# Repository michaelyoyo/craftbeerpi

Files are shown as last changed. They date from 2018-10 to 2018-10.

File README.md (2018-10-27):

# CraftBeerPi

This project is shamelessly forked from https://github.com/Manuel83/craftbeerpi

This fork is intended to add support for a few new sensors and for my custom HERMS
controller PCB.

The PCB contains
-2x MAX31865 RTD Amplifiers
-1x EzoPh Amplifier
-2x Pump/Heater Outputs
-A bunch of LEDs
-Automatic control of a 12v Power Supply
-An expansion connector because I can't think of everything

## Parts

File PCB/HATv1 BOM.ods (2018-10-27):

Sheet: HATv1
Part | Value | Package | Description | Source/PN | Footprint correct? | Notes
C1 | 0.1uF | 0603 | 5v buck boost | have | y
C2 | 100uF | PANASONIC_E | Main input filter cap | have | y | --Probably need more capacitance (6A max input current...) | -Check package
C3 | 10uF | 0805 | Buck filter cap | have | y
C4 | 0.1uF | 0603 | buck filter cap | have | y
C5 | 22uF | 1210 | buck output cap | have | y
C6 | 22uF | 1210 | buck output cap | have | y
C7 | 22uF | 1210 | buck output cap | have | y
C8 | 75pF | 0603 | buck ff cap | have | y
C9 | 10uF | 0805 | 3.3vsb ldo input | have | y
C10 | 1uF | 0603 | 3.3vsb ldo output | have | y
C11 | 47uF | 3528 | rPi 5v input | have | y | -1206
C12 | 0.1uF | 0603 | eeprom decoupling | have | y
C13 | 0.1uF | 0603 | pwm decoupling | have | y
C14 | 3.3u | 0603 | isense1 filter | have | y
C15 | 3.3u | 0603 | isense2 filter | have | y
C16 | 0.1u | 0603 | rtd1 decoupling | have | y
C17 | 0.1u | 0603 | rtd1 decoupling | have | y
C18 | 0.1u | 0603 | rtd2 decoupling | have | y
C19 | 0.1u | 0603 | rtd2 decoupling | have | y
C20 | 100n | 0603 | rtd1 filter | have | y
C21 | 100n | 0603 | rtd2 filter | have | y
C22 | 10uF | 1206 | ezoph decoupling | have | y
D1 | 250mA/100V | SMA | pump1 flyback | have | y
D2 | 250mA/100V | SMA | pump2 flyback | have | y
F1 | 7.5A | 1206 | main input | 693-3413.0224.22 | y
F2 | 1A | 1206 | 5vbuck input | 530-0ZCG0150BF2C | y
F3 | 25mA | 1206 | 3.3vsb input | have | y |  | -I have 50mA through hole fuses
J1 |  |  | 6pin PSU input | 710-691305140006 | y | 710-691363110006
J4 | 20 Pin low profile smt header | 2x20 0.1” Header | rpi header | 200-HLE12002GDVA | y
J5 | 1.27mm | 24pin 0.05” FFC | expansion connector | 538-502244-2430 | y | 538-15021-0424
J6 |  | 5mm Terminal Block | pump1 | 710-691305140002 | y | 710-691363110002
J7 |  | 5mm Terminal Block | pump2 | 710-691305140002 | y | 710-691363110002
J8 |  | 3pin Molex | rtd1 | 538-22-04-1031 | y | 538-22-01-1032 | 538-08-50-0113-CT
J9 |  | 3pin Molex | rtd2 | 538-22-04-1031 | y | 538-22-01-1032
J10 | BNCPTH | BNC | ezoph | have | y
L1 | 33uH | srp1265a | 5v buck | have | y
LED1 | red | 0603 | adc alert (pump overcurrent) | 859-LTST-C191KRKT | y
LED2 | green | 0603 | gpled0 | have | y
LED3 | red | 0603 | gpled1 | 859-LTST-C191KRKT | y
LED4 | green | 0603 | rtd1 good | have | y
LED5 | green | 0603 | rtd2 good | have | y
LED6 | green | 0603 | phgood | have | y
LED7 | blue | 0603 | 3.3v rail | have | y
LED8 | blue | 0603 | 5v rail | have | y
LED9 | blue | 0603 | 12v rail | have | y
Q1 | MOSFETSON5X6 | SON5X6MM | pump1 | have | y
Q2 | MOSFETSON5X6 | SON5X6MM | pump2 | have | y
Q3 | 220mA/50V/3.5Î© | SOT23-3 | adc alert | 621-DMG6968U-7 | y
R1 | 511k | 0603 | 5v buck enable | have | y
R2 | 49.9 | 0603 | 5v buck feedback | have | y | <1%
R3 | 100k | 0603 | 5v buck enable | have | y
R4 | 100k | 0603 | 5v buck feedback | have | y | <1%
R5 | 13.3k | 0603 | 5v buck feedback | have | y | <1%
R6 | 180 | 0603 | pon opto current limit | have | y
R7 | 887k | 0603 | pon delay div set | 660-RN73H1JTD8873B25 | y | <1%
R8 | 715k | 0603 | pon delay set | 660-RN73H1JD7233F100 | y | 725k, make sure it still works
R9 | 1M | 0603 | pon delay div set | have | y | <1%
R10 | 3.9k | 0603 | i2c pullup | have | y
R11 | 3.9k | 0603 | i2c pullup | have | y
R12 | 1k | 0603 | eeprom wp pullup | have | y
R13 | 3.9k | 0603 | eeprom i2c pullup | have | y
R14 | 3.9k | 0603 | eeprom i2c pullup | have | y
R15 | 180 | 0603 | led ilim | have | y | -all leds, calculate proper current limit
R16 | 180 | 0603 | led ilim | have | y
R17 | 180 | 0603 | led ilim | have | y
R18 | 180 | 0603 | led ilim | have | y
R19 | 180 | 0603 | led ilim | have | y
R20 | 180 | 0603 | led ilim | have | y
R21 | 50m | 1206 | pump1 shunt | 588-LVK12R050DER | y | <.5%
R22 | 50m | 1206 | pump2 shunt | 588-LVK12R050DER | y | <.5%
R23 | 180 | 0603 | led ilim | have | y
R24 | 180 | 0603 | led ilim | have | y
R25 | 180 | 0603 | led ilim | have | y
R26 | 3.3k | 0603 | adc alert pullup | have | y
R27 | 330 | 0603 | isense1 filter | have | y | <1%
R28 | 330 | 0603 | isense2 filter | have | y | <1%
R29 | 400 .1% | 0603 | rtd1 reference | 71-PAT0603E4000BST1 | y | <.1%
R30 | 400 .1% | 0603 | rtd2 reference | 71-PAT0603E4000BST1 | y | <.1%
S1 |  | 12mm Tact Switch PTH | pon switch | 611-PTS125SK85LFS | y
U1 |  | SOT23-6 | 5v buck | have | y
U2 | NCP715 | SC70 | 3.3vsb ldo | 863-NCP715SQ33T2G | y
U3 | LT6994 | SOT23-6 | pon off delay | 584-C6994MPS6-1TMPF | y
U4 | ILD213T-IDL213T | SO08 | pon opto | 782-ILD213T | y
U5 | LT4358LTC4358CFE | TSSOP-16 | rPi ideal diode | 584-LTC4358CFE#PBF | y
U6 | CAT24C256 | SO8 | rPi eeprom | have | y
U7 | PCA9685 | TSSOP-28_4MM | 16-channel 12-bit PWM | have | y
U8 | ADS1015 | MSOP10 | ADS1015 12-BIT ADC | have | y
U9 | MAX31865 | TQFN20 | rtd1 | sample from maxim | y
U10 | MAX31865 | TQFN20 | rtd2 | sample from maxim | y
U11 | EZOPH | EZOPH | ph measurement | have | y | -update footprint

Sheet: Sheet2
R6 | 180 | 0603 | pon opto current limit | have | y
R15 | 180 | 0603 | led ilim | have | y | -all leds, calculate proper current limit
R16 | 180 | 0603 | led ilim | have | y
R17 | 180 | 0603 | led ilim | have | y
R18 | 180 | 0603 | led ilim | have | y
R19 | 180 | 0603 | led ilim | have | y
R20 | 180 | 0603 | led ilim | have | y
R23 | 180 | 0603 | led ilim | have | y
R24 | 180 | 0603 | led ilim | have | y
R25 | 180 | 0603 | led ilim | have | y
R27 | 330 | 0603 | isense1 filter | have | y | <1%
R28 | 330 | 0603 | isense2 filter | have | y | <1%
R10 | 3.9k | 0603 | i2c pullup | have | y
R11 | 3.9k | 0603 | i2c pullup | have | y
R13 | 3.9k | 0603 | eeprom i2c pullup | have | y
R14 | 3.9k | 0603 | eeprom i2c pullup | have | y

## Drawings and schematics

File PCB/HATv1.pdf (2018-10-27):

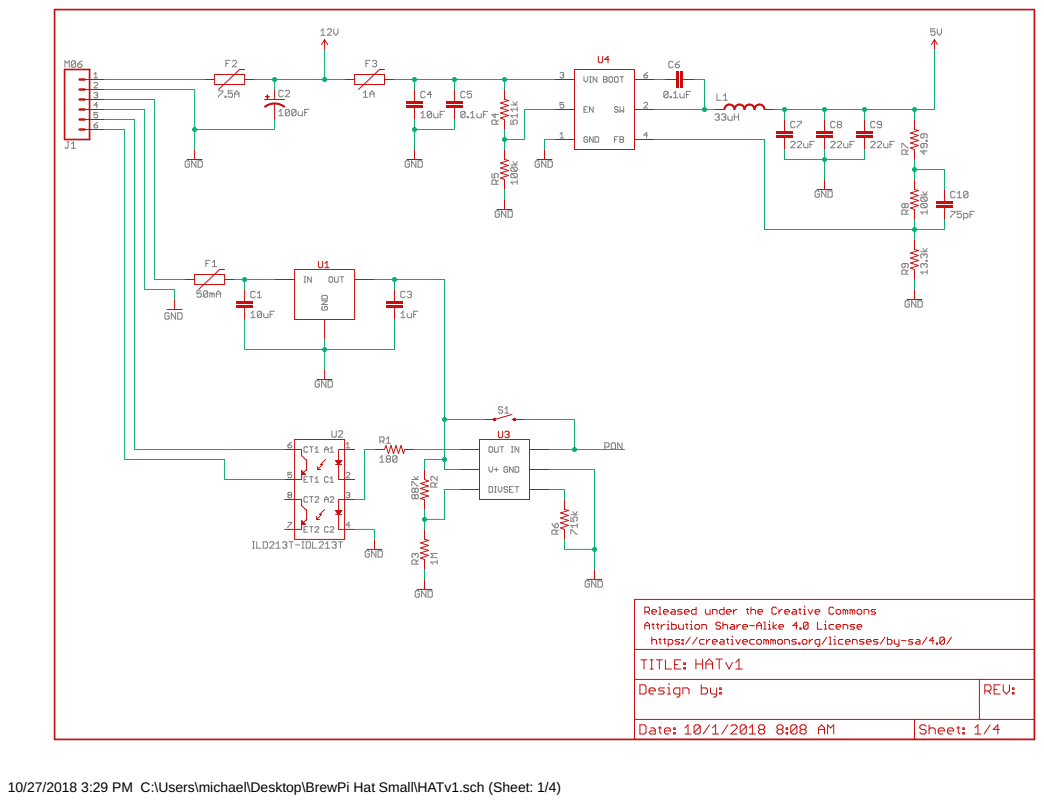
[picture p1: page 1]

10/27/2018 3:29 PM C:\Users\michael\Desktop\BrewPi Hat Small\HATv1.sch (Sheet: 1/4)

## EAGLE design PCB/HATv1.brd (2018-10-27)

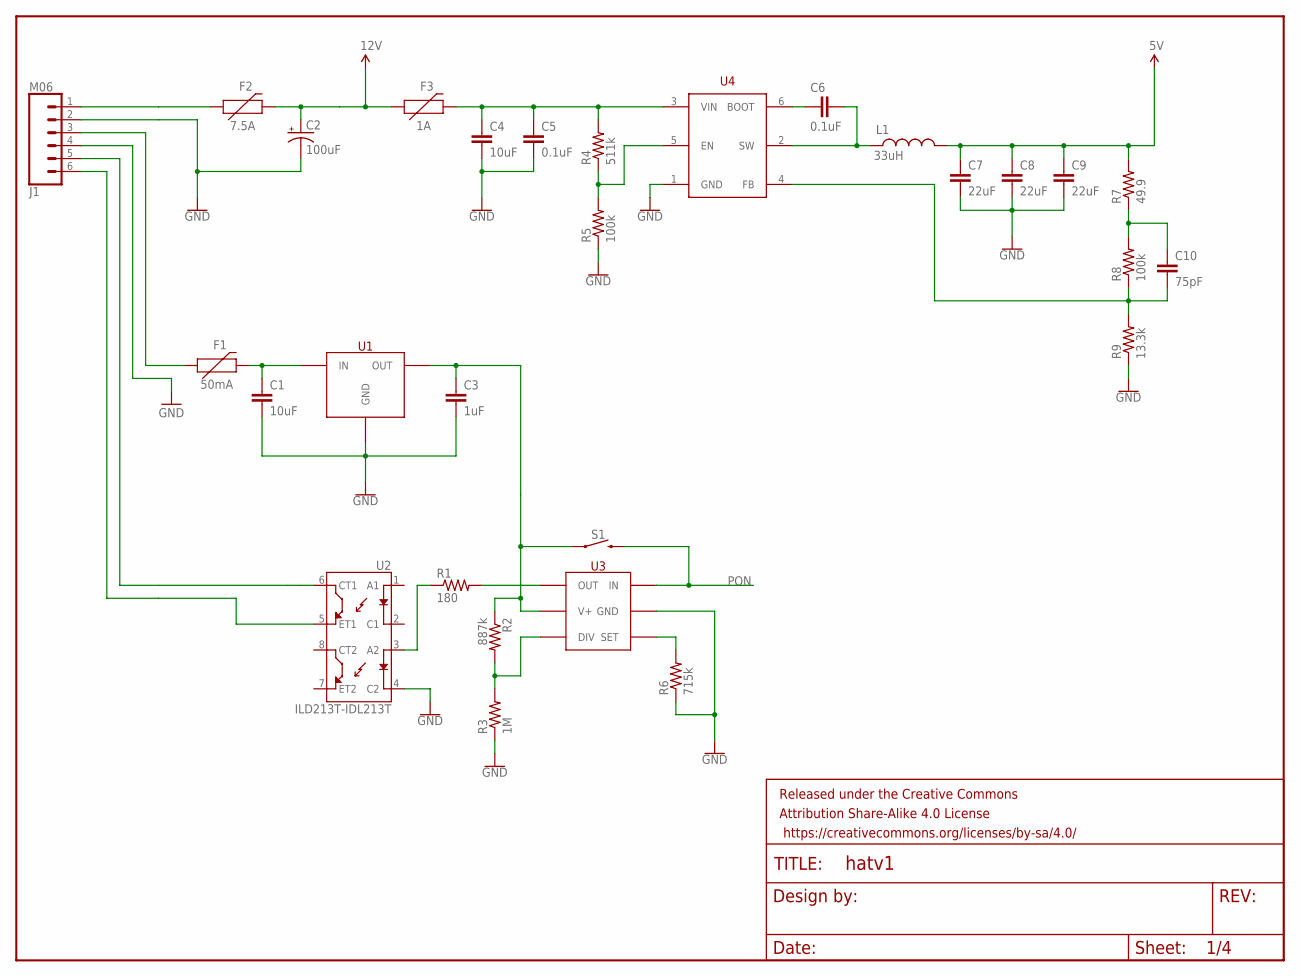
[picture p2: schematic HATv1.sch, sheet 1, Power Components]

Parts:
C1, C4: 10uF; 0805
C2: 100uF; PANASONIC_E
C3: 1uF; 0603-CAP
C5, C6: 0.1uF; 0603-CAP
C7, C8, C9: 22uF; 1210
C10: 75pF; 0603-CAP
F1: 50mA; PTH
F2: 7.5A; 1206
F3: 1A; 2010
FRAME1: FRAME-LETTERNO_PACKAGE; DUMMY
J1: M06; SCREWTERMINAL-3.5MM-6
L1: 33uH; SRP1265A
R1: 180; 0603-RES
R2: 887k; 0603-RES
R3: 1M; 0603-RES
R4: 511k; 0603-RES
R5, R8: 100k; 0603-RES
R6: 715k; 0603-RES
R7: 49.9; 0603-RES
R9: 13.3k; 0603-RES
S1: MOMENTARY-SWITCH-SPST-SMD-12MM; TACTILE_SWITCH_SMD_12MM
U1: NCP715; SC70
U2: ILD213T-IDL213T; SO08
U3: LT6994; SOT23-6
U4: TPS54302; SOT23-6

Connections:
5V: C7.1, C8.1, C9.1, L1.P$2 (2), R7.2; also elsewhere on the board
12V: C2.+, F2.2, F3.1; also elsewhere on the board
GND: C1.2, C2.-, C3.2, C4.2, C5.2, C7.2, C8.2, C9.2, J1.2, J1.4, R3.1, R5.1, R6.1, R9.1, U1.2 (GND), U2.4 (C2), U3.2 (GND), U4.1 (GND); also elsewhere on the board
unnamed: R1.1, U2.3 (A2)
unnamed: C6.1, U4.6 (BOOT)
unnamed: C6.2, L1.P$1 (1), U4.2 (SW)
unnamed: C10.1, R7.1, R8.2
unnamed: C10.2, R8.1, R9.2, U4.4 (FB)
unnamed: R4.1, R5.2, U4.5 (EN)
unnamed: J1.6, U2.5 (ET1)
unnamed: J1.5, U2.6 (CT1)
unnamed: R1.2, U3.6 (OUT)
unnamed: R2.2, R3.2, U3.4 (DIV)
unnamed: R6.2, U3.3 (SET)
unnamed: C3.1, R2.1, S1.1, U1.5 (OUT), U3.5 (V+)
unnamed: C1.1, F1.P$2 (2), U1.4 (IN)
unnamed: F1.P$1 (1), J1.3
unnamed: C4.1, C5.1, F3.2, R4.2, U4.3 (VIN)
unnamed: F2.1, J1.1
PON: S1.3 (2), U3.1 (IN); also elsewhere on the board

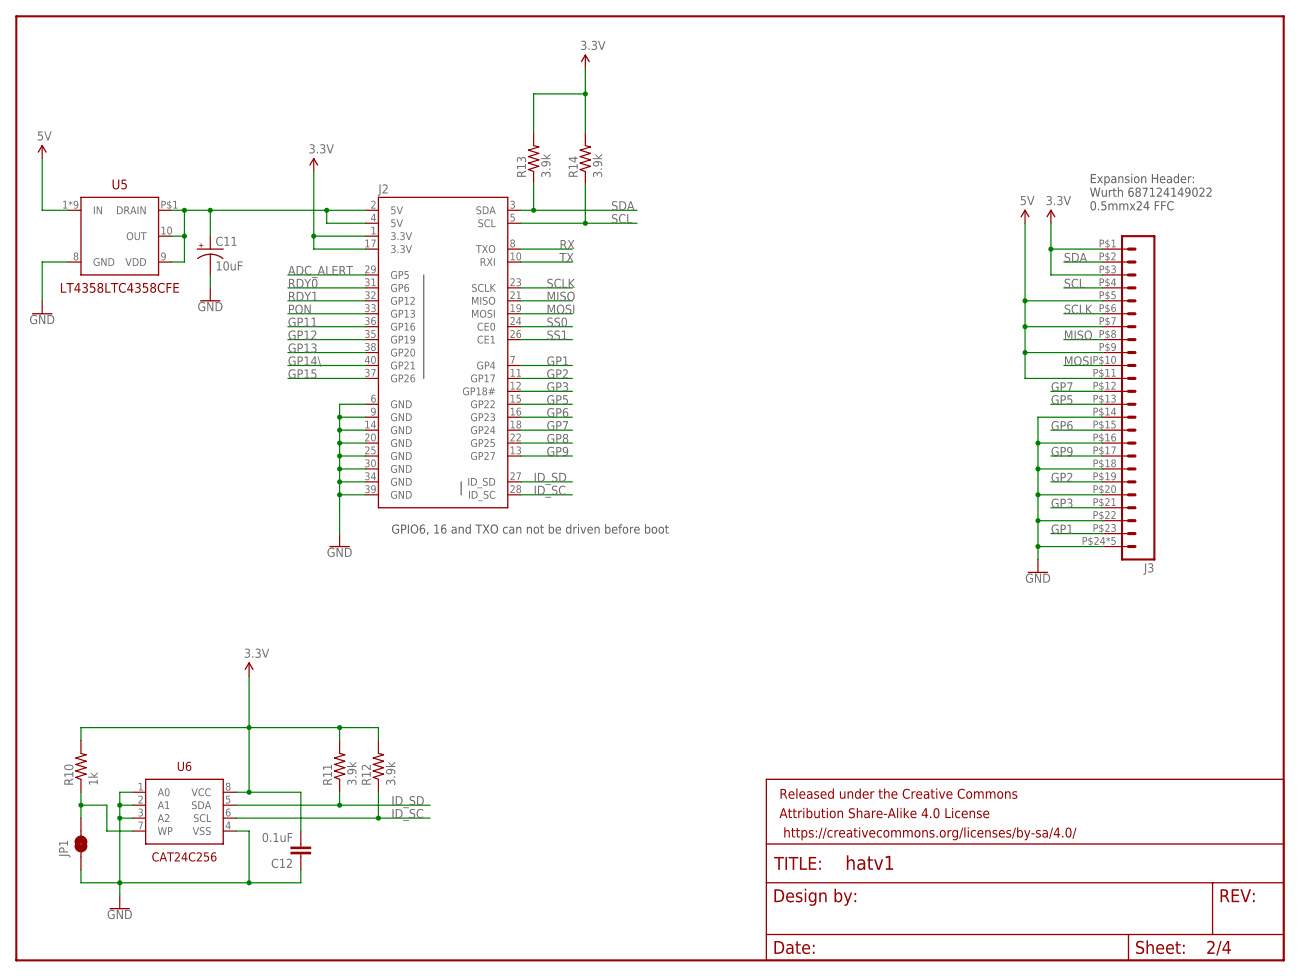
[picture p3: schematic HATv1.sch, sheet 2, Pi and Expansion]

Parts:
C11: 10uF; EIA3216
C12: 0.1uF; 0603-CAP
FRAME2: FRAME-LETTERNO_PACKAGE; DUMMY
J2: RASPBERRYPI-40-PIN-GPIO2X20PASSTHROUGH; 1X24SAMTEC
J3: M24FFC; FFC_24
JP1: JUMPER-PAD-2-NC_BY_TRACE; PAD-JUMPER-2-NC_BY_TRACE_YES_SILK
R10: 1k; 0603-RES
R11, R12, R13, R14: 3.9k; 0603-RES
U5: LT4358LTC4358CFE; TSSOP-16
U6: CAT24C256; SO8

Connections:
3.3V: C12.2, J2.1 (3.3V), J2.17 (3.3V), J3.P$1 (2), J3.P$3 (4), R10.2, R11.2, R12.2, R13.2, R14.2, U6.8 (VCC); also elsewhere on the board
5V: J3.P$5 (6), J3.P$7 (8), J3.P$9 (10), J3.P$11 (12), U5.1 (IN), U5.2 (IN), U5.3 (IN), U5.4 (IN), U5.12 (IN), U5.13 (IN), U5.14 (IN), U5.15 (IN), U5.16 (IN); also elsewhere on the board
ADC_ALERT: J2.29 (GP5); also elsewhere on the board
GND: C11.-, C12.1, J2.6 (GND), J2.9 (GND), J2.14 (GND), J2.20 (GND), J2.25 (GND), J2.30 (GND), J2.34 (GND), J2.39 (GND), J3.P$14 (15), J3.P$16 (17), J3.P$18 (19), J3.P$20 (21), J3.P$22 (23), J3.P$24 (25), J3.P$25 (25), J3.P$26 (25), J3.P$27 (25), J3.P$28 (25), JP1.1, U5.8 (GND), U6.1 (A0), U6.2 (A1), U6.3 (A2), U6.4 (VSS); also elsewhere on the board
GP1: J2.7 (GP4), J3.P$23 (24)
GP2: J2.11 (GP17), J3.P$19 (20)
GP3: J2.12 (GP18#), J3.P$21 (22)
GP5: J2.15 (GP22), J3.P$13 (14)
GP6: J2.16 (GP23), J3.P$15 (16)
GP7: J2.18 (GP24), J3.P$12 (13)
GP8: J2.22 (GP25)
GP9: J2.13 (GP27), J3.P$17 (18)
GP11: J2.36 (GP16)
GP12: J2.35 (GP19)
GP13: J2.38 (GP20)
GP14\: J2.40 (GP21)
GP15: J2.37 (GP26)
ID_SC: J2.28 (ID_SC), R12.1, U6.6 (SCL)
ID_SD: J2.27 (ID_SD), R11.1, U6.5 (SDA)
MISO: J2.21 (MISO), J3.P$8 (9); also elsewhere on the board
MOSI: J2.19 (MOSI), J3.P$10 (11); also elsewhere on the board
unnamed: JP1.2, R10.1, U6.7 (WP)
unnamed: C11.+, J2.2 (5V), J2.4 (5V), U5.9 (VDD), U5.10 (OUT), U5.P$1 (DRAIN)
PON: J2.33 (GP13); also elsewhere on the board
RDY0: J2.31 (GP6); also elsewhere on the board
RDY1: J2.32 (GP12); also elsewhere on the board
RX: J2.8 (TXO); also elsewhere on the board
SCL: J2.5 (SCL), J3.P$4 (5), R14.1; also elsewhere on the board
SCLK: J2.23 (SCLK), J3.P$6 (7); also elsewhere on the board
SDA: J2.3 (SDA), J3.P$2 (3), R13.1; also elsewhere on the board
SS0: J2.24 (CE0); also elsewhere on the board
SS1: J2.26 (CE1); also elsewhere on the board
TX: J2.10 (RXI); also elsewhere on the board

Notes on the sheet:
GPIO6, 16 and TXO can not be driven before boot
Expansion Header: Wurth 687124149022 0.5mmx24 FFC

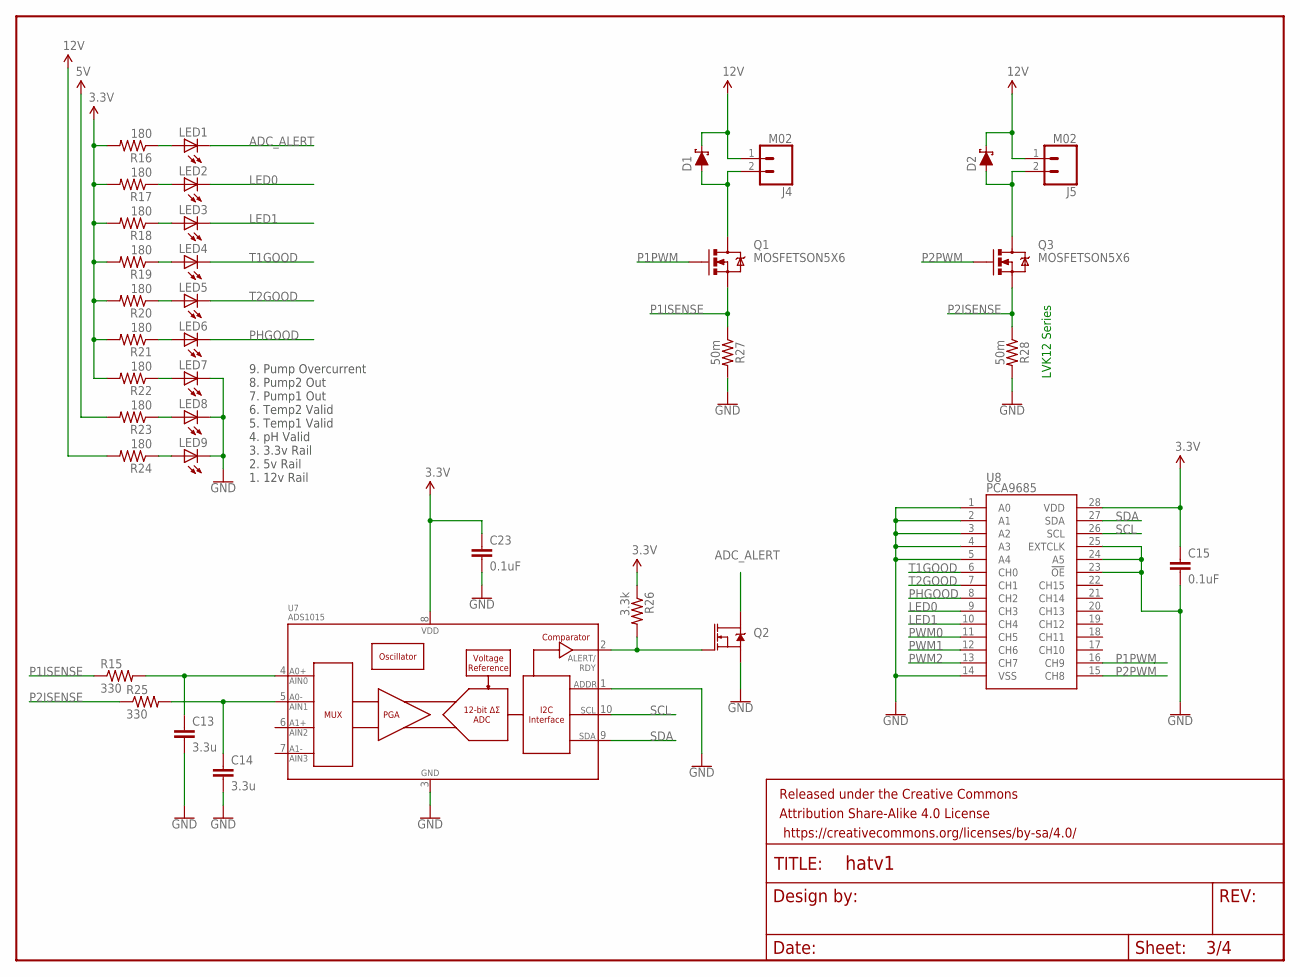
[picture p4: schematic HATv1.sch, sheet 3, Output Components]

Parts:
C13, C14: 3.3u; 0603
C15, C23: 0.1uF; 0603-CAP
D1, D2: DIODE-SCHOTTKY-B340A; SMA-DIODE
FRAME3: FRAME-LETTERNO_PACKAGE; DUMMY
J4, J5: M02; SCREWTERMINAL-3.5MM-2
LED1, LED2, LED3, LED4, LED5, LED6, LED7, LED8, LED9: LEDCHIP-LED0603; CHIP-LED0603
Q1, Q3: MOSFETSON5X6; SON5X6MM
Q2: MOSFET-NCH-BSS138; SOT23-3
R15, R25: 330; 0603-RES
R16, R17, R18, R19, R20, R21, R22, R23, R24: 180; 0603-RES
R26: 3.3k; 0603-RES
R27, R28: 50m; 1206
U7: ADS1015; MSOP10
U8: PCA9685; TSSOP-28_4MM

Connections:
3.3V: C15.1, C23.1, R16.2, R17.2, R18.2, R19.2, R20.2, R21.2, R22.2, R26.1, U7.8 (VDD), U8.28 (VDD); also elsewhere on the board
5V: R23.2; also elsewhere on the board
12V: D1.C, D2.C, J4.1, J5.1, R24.2; also elsewhere on the board
ADC_ALERT: LED1.C, Q2.3 (D); also elsewhere on the board
GND: C13.2, C14.2, C15.2, C23.2, LED7.C, LED8.C, LED9.C, Q2.2 (S), R27.2, R28.2, U7.1 (ADDR), U7.3 (VSS), U8.1 (A0), U8.2 (A1), U8.3 (A2), U8.4 (A3), U8.5 (A4), U8.14 (VSS), U8.23 (!OE), U8.24 (A5), U8.25 (EXTCLK); also elsewhere on the board
LED0: LED2.C, U8.9 (CH3)
LED1: LED3.C, U8.10 (CH4)
unnamed: LED1.A, R16.1
unnamed: D1.A, J4.2, Q1.P$5 (D), Q1.P$6 (D), Q1.P$7 (D), Q1.P$8 (D), Q1.P$9 (D)
unnamed: D2.A, J5.2, Q3.P$5 (D), Q3.P$6 (D), Q3.P$7 (D), Q3.P$8 (D), Q3.P$9 (D)
unnamed: C13.1, R15.2, U7.4 (AIN0)
unnamed: Q2.1 (G), R26.2, U7.2 (ALERT/RDY)
unnamed: LED2.A, R17.1
unnamed: LED3.A, R18.1
unnamed: LED4.A, R19.1
unnamed: LED5.A, R20.1
unnamed: LED6.A, R21.1
unnamed: LED7.A, R22.1
unnamed: LED8.A, R23.1
unnamed: LED9.A, R24.1
unnamed: C14.1, R25.2, U7.5 (AIN1)
P1ISENSE: Q1.P$1 (S), Q1.P$2 (S), Q1.P$3 (S), R15.1, R27.1
P1PWM: Q1.P$4 (G), U8.16 (CH9)
P2ISENSE: Q3.P$1 (S), Q3.P$2 (S), Q3.P$3 (S), R25.1, R28.1
P2PWM: Q3.P$4 (G), U8.15 (CH8)
PHGOOD: LED6.C, U8.8 (CH2)
PWM0: U8.11 (CH5)
PWM1: U8.12 (CH6)
PWM2: U8.13 (CH7)
SCL: U7.10 (SCL), U8.26 (SCL); also elsewhere on the board
SDA: U7.9 (SDA), U8.27 (SDA); also elsewhere on the board
T1GOOD: LED4.C, U8.6 (CH0)
T2GOOD: LED5.C, U8.7 (CH1)

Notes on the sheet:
9. Pump Overcurrent 8. Pump2 Out 7. Pump1 Out 6. Temp2 Valid 5. Temp1 Valid 4. pH Valid 3. 3.3v Rail 2. 5v Rail 1. 12v Rail
LVK12 Series

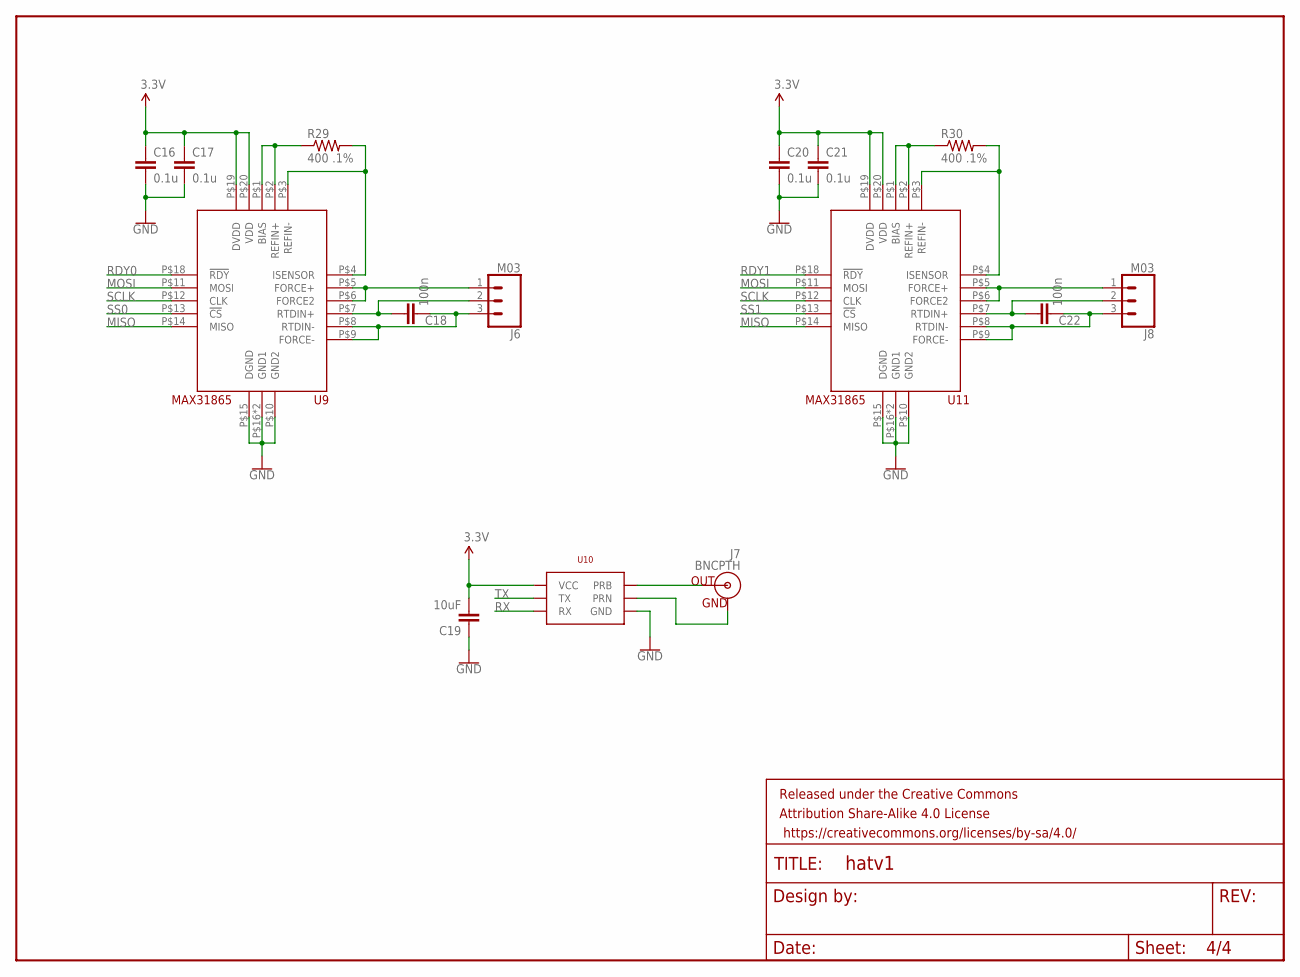
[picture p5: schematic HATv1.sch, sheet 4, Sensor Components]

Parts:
C16, C17, C20, C21: 0.1u; 0603-CAP
C18, C22: 100n; 0603-CAP
C19: 10uF; 1206
FRAME4: FRAME-LETTERNO_PACKAGE; DUMMY
J6, J8: M03; 1X03
J7: BNCPTH; BNC
R29, R30: 400 .1%; 0603-RES
U9, U11: MAX31865; TQFN20
U10: EZOPH

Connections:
3.3V: C16.1, C17.1, C19.2, C20.1, C21.1, U9.P$19 (DVDD), U9.P$20 (VDD), U10.VCC, U11.P$19 (DVDD), U11.P$20 (VDD); also elsewhere on the board
GND: C16.2, C17.2, C19.1, C20.2, C21.2, U9.P$10 (GND2), U9.P$15 (DGND), U9.P$16 (GND1), U9.P$21 (GND1), U10.GND, U11.P$10 (GND2), U11.P$15 (DGND), U11.P$16 (GND1), U11.P$21 (GND1); also elsewhere on the board
MISO: U9.P$14 (MISO), U11.P$14 (MISO); also elsewhere on the board
MOE2: J6.1, U9.P$5 (FORCE+), U9.P$6 (FORCE2)
MOE3: J8.1, U11.P$5 (FORCE+), U11.P$6 (FORCE2)
MOSI: U9.P$11 (MOSI), U11.P$11 (MOSI); also elsewhere on the board
unnamed: J7.S (OUT), U10.PRB
unnamed: J7.GND, U10.PGND (PRN)
unnamed: R29.1, U9.P$1 (BIAS), U9.P$2 (REFIN+)
unnamed: R29.2, U9.P$3 (REFIN-), U9.P$4 (ISENSOR)
unnamed: C18.2, J6.3, U9.P$8 (RTDIN-), U9.P$9 (FORCE-)
unnamed: C18.1, J6.2, U9.P$7 (RTDIN+)
unnamed: R30.1, U11.P$1 (BIAS), U11.P$2 (REFIN+)
unnamed: R30.2, U11.P$3 (REFIN-), U11.P$4 (ISENSOR)
unnamed: C22.2, J8.3, U11.P$8 (RTDIN-), U11.P$9 (FORCE-)
unnamed: C22.1, J8.2, U11.P$7 (RTDIN+)
RDY0: U9.P$18 (!RDY); also elsewhere on the board
RDY1: U11.P$18 (!RDY); also elsewhere on the board
RX: U10.RX; also elsewhere on the board
SCLK: U9.P$12 (CLK), U11.P$12 (CLK); also elsewhere on the board
SS0: U9.P$13 (!CS); also elsewhere on the board
SS1: U11.P$13 (!CS); also elsewhere on the board
TX: U10.TX; also elsewhere on the board

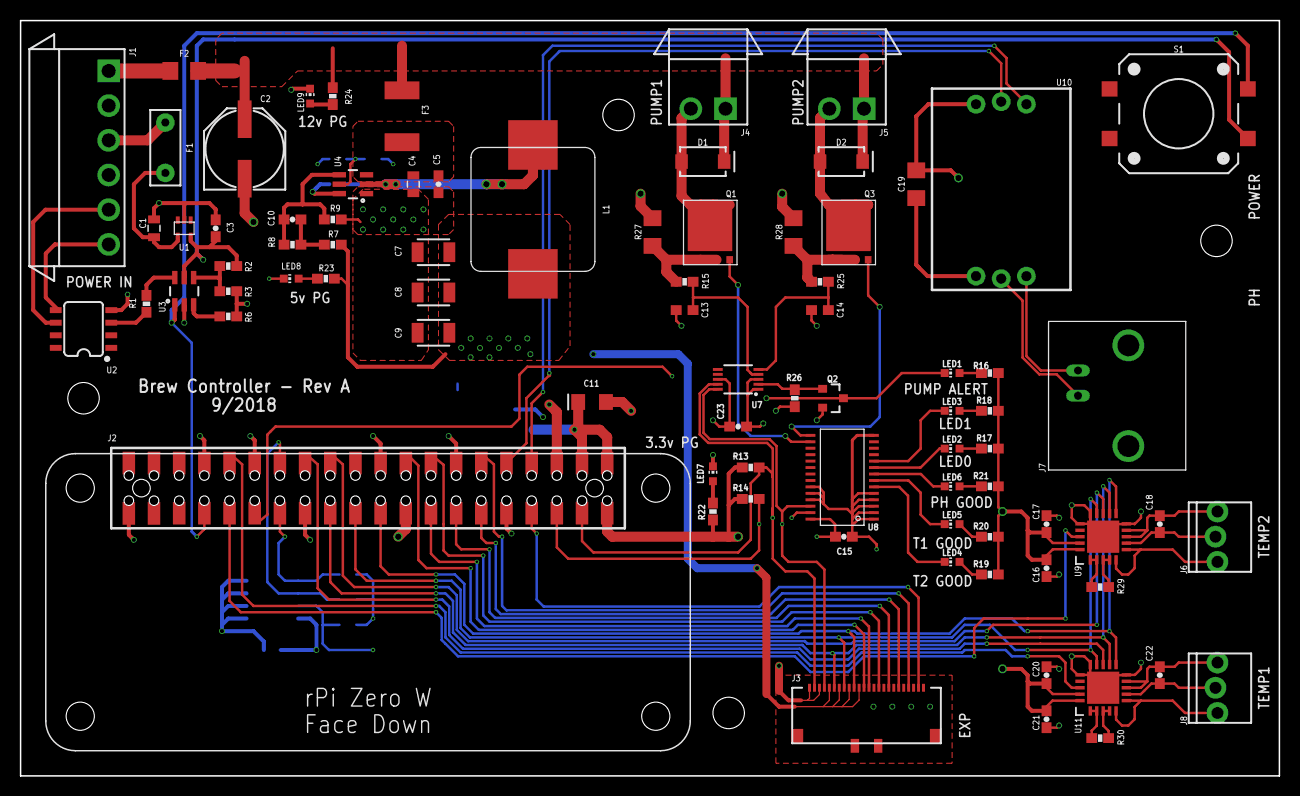
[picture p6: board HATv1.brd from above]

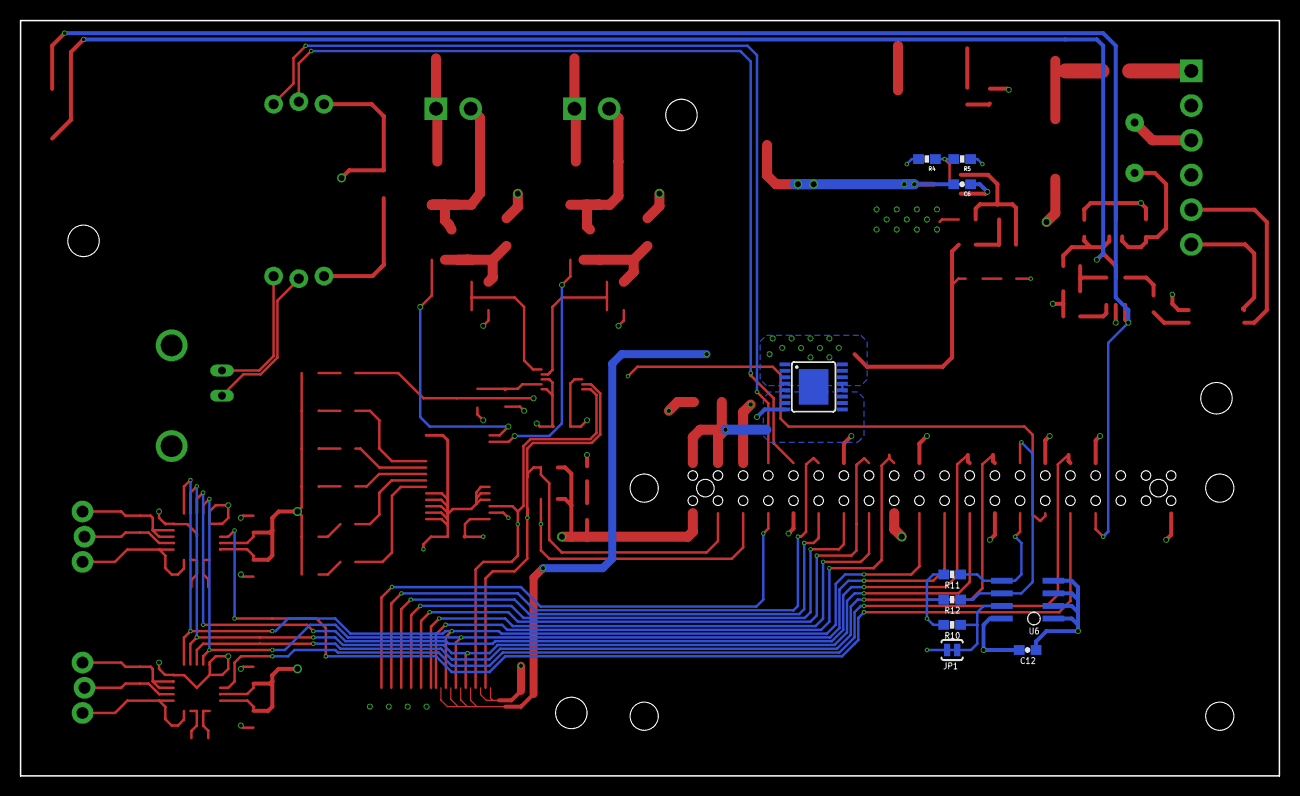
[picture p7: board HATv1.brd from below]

Board: 4 copper layers, 127.0 x 76.2 mm, 96 parts (10 on the bottom side), 79 nets.

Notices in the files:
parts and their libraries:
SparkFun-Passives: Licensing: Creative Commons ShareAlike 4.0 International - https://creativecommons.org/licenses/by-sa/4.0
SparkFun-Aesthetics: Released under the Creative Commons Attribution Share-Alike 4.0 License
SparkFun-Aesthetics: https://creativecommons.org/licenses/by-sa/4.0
